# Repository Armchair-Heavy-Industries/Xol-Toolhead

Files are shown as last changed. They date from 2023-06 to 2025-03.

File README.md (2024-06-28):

[][cc-by-nc-sa]

# Xol Toolhead
Xol Toolhead is the evolution of 'Mantis Xol 2' (<https://github.com/Armchair-Engineering/Mantis-Xol>).<br/>
Aimed at modularity and quality of life improvements for installation and serviceability.<br/>
We have left the mantis carriage behind, and thus are now just Xol sans Mantis. Don't worry, it's still a bit ugly. We wouldn't fix that.

Project lead: ko-fi (https://ko-fi.com/O5O5OCC0K) [DW-Tas](https://github.com/DW-Tas)

Join me on Discord (https://discord.gg/armchairengineeringsux)

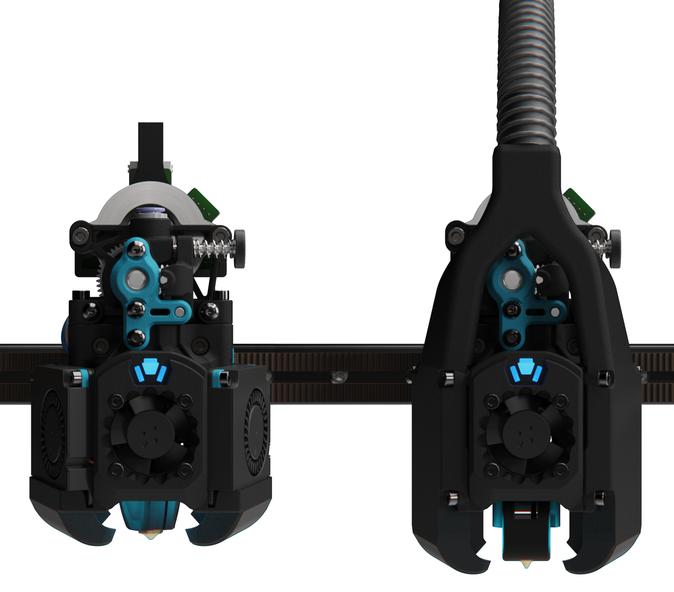
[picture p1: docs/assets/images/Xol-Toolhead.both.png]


## Go to the /docs
All of the documentation has been moved to /docs to help keep the repo organised (crazy I know) and enable future things.
* [Full README](docs/README.md)
  * [Bill of Materials (BOM)](docs/BOM.md)
  * [Printing parts](docs/printing.md)
  * [Carriage assembly](docs/xol_carriage_assembly.md)
  * [Toolhead assembly](docs/toolhead_assembly.md)

<br/><br/>
You can help support the development of Armchair projects.<br/>
Donate at https://ko-fi.com/armchair<br/>
ko-fi (https://ko-fi.com/armchair)
<br/> <br/>

This work is licensed under a
[Creative Commons Attribution-NonCommercial-ShareAlike 4.0 International License][cc-by-nc-sa].

[][cc-by-nc-sa]

[cc-by-nc-sa]: http://creativecommons.org/licenses/by-nc-sa/4.0/
[cc-by-nc-sa-image]: https://licensebuttons.net/l/by-nc-sa/4.0/88x31.png
[cc-by-nc-sa-shield]: https://img.shields.io/badge/License-CC%20BY--NC--SA%204.0-lightgrey.svg

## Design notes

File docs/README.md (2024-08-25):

[][cc-by-nc-sa]

# Xol Toolhead
Xol Toolhead is the evolution of 'Mantis Xol 2' (<https://github.com/Armchair-Engineering/Mantis-Xol>).<br/>
Aimed at modularity and quality of life improvements for installation and serviceability.<br/>
We have left the mantis carriage behind, and thus are now just Xol sans Mantis. Don't worry, it's still a bit ugly. We wouldn't fix that.

Project lead: ko-fi (https://ko-fi.com/O5O5OCC0K) [DW-Tas](https://github.com/DW-Tas)

Join me on Discord (https://discord.gg/armchairengineeringsux)



## What's new
`Xol-Toolhead Release [2024-06-19]`
### Major update
* Quality of life improvements
  * Toolhead
    * Combined multiple printed parts to simplify assembly
    * No more M2 or M2.5 heatset inserts
    * Part cooling fans slide into the top of the ducts are are secured with 2x M2.5x8 SHCS per fan
      * Hardware reduced from 8x M2 heatsets + 8 M2 screws to just 4 M2.5 screws
    * HE Fan now uses 4x M2.5x16 SHCS (previous M2.5x20 should still work)
    * All four hotend mounting screws can now be used with Rapido and Dragon UHF when using Sherpa-Mini Extruder
  * Carriage
    * Xol Carriage is now a single piece print
    * Belt clips are now the Archetype belt clip system
    * Internal path added for probe wires
* BOM changes
  * Toolhead
    * Removed:
      * M2 and M2.5 heatsets (except for X endstop)
      * M2 Screws (except for X endstop)
    * Extruder mount front 2 SHCS now 16mm (previously 20mm)
  * Carriage
    * All versions now attach to MGN rail with M3x8 SHCS (MGN12 previously required M3x6 BHCS)
    * Archetype belt clips require 4mm OD, 0.45mm wall width tube
      * 2x 22.5mm lengths
      * 'Has been tested with 4/3mm PTFE tube and seems OK but harder to install'
    * Belt pins are now all M3x30 for all carriage/belt combinations
      * Cut down screws now OK due to the metal tube protecting the belts
    * Added:
      * Large M3 washers and 2x M3x8 SHCS for MGN Carriage clamps (not optional, required for carriage strength)
* Tool Requirement
  * Tightening the M3 SHCS of the toolhead "feet" to the carriage requires a M2.5 ball head hex driver. `This is due to the requirement to tighten these screws from a slight angle.`
<details>
<summary><strong>Previous updates</strong> [click to expand]</summary>
<br/>

`Xol-Toolhead Release 2023-12-21`
[Historic Repo Link](https://github.com/Armchair-Heavy-Industries/Xol-Toolhead/tree/b5e52d79f11106338cad1ea619fc55be004061d5)
* Quality of life improvements
  * Cable routing holes are now on both sides of the toolhead
  * Cable routing holes can now fit MF3.0 commonly used on hotends
  * Awkward M3 Heatset insert replaced with easier to install M3 hex nut for front extruder mount connection
  * Rapido hotend mounting points rotated to improve wire routing
* Minimal BOM change
  * 1x M3 Hex Nut replaces 1x M3 Heatset Insert
  * 1x M3x6 BHCS replaces 1x M3x8 BHCS
* Reworked Extruder mount to Hotend mount interface
  * Old Hotend mounts will not work with new Extruder mounts and vice-versa

`Xol-Toolhead Release 2023-09-15`
[Historic Repo Link](https://github.com/Armchair-Heavy-Industries/Xol-Toolhead/tree/18acdc784e08c6703e5be316338cb8c8f26e0477)
* Modular approach to hotend mounts and extruders
  * Hotend mounts and extruder mounts are now separate parts
  * Extruder mounts incorporate the old Xol-Carriage or TAP adapter plates (same number of printed parts overall)
  * "Xol with bones" option: Add some screws for extra rigidity in the hotend mount
* Minimal BOM change
  * 1x M3x8 BHCS
  * 1x M3 Heatset
  * Optional "bones"
    * 2x M2x30 SHCS
    * 2x M2 Heatset
* Xol-Carriage update
  * Stronger belt clips
  * bigger probe cable channel with cable tie slot

`Xol-Toolhead Release 2023-07-14`
[Historic Repo Link](https://github.com/Armchair-Heavy-Industries/Xol-Toolhead/tree/bd63772155dfab692449fd498208c855561d44cf)
* Standardised hotend mounts around the Voron Design CW2/TAP carriage bolt hole pattern.
  * This approach reduces the number of hotend mounts and ducts by half - You don't have to search for TAP or non-TAP and we don't have to maintain twice as many parts
* Xol-Carriage
  * A new carriage built for Xol-Toolhead
  * Uses metal pins and a belt clip to secure the belts instead of having them squashed between mgn9/12 carriage and toolhead carriage
  * Improved serviceability - remove the toolhead from the carriage without disassembly in the printer. Unless you use Voron TAP or refuse to buy M2.5 hardware for Xol Carriage. Buy the m2.5 hardware, it's worth it trust us.
  * Modular probe mounting system - change probes without changing the whole carriage _`*Except for KlickyNG`_
* These carriage changes mean you can use any carriage that a Stealthburner bolts onto. (Our Xol-Carriage, or the stock voron carriage even.)
</details>

## Supported hardware
### Hotends
* Rapido HF
* Rapido UHF
* DropEffect XG
* DropEffect NeXtG
* Red Lizard K1-UHF
* Dragon UHF / UHF-Mini
* Dragon Standard / High Flow
* Dragon Ace
* Revo Voron
* NF-Crazy Volcano (or standard with v6 melt zone extender) `NF-Crazy with standard wide block no longer supported without extender`
* Others via User mods including [Bambulab](https://github.com/Armchair-Heavy-Industries/Armchair-Usermods/tree/main/files/Xol-Toolhead/BambuLab_Xol_HE_Mount)

### Extruders
* Sherpa-Mini
* Annex Double Folded Ascender
* Galileo G2SA *
* WristWatch G2 *
* WristWatch BMG
* Escapement (experimental)
* Vz-Hextrudort-Low
* LGX-Lite
* Orbiter v2.0

`⚠️ * G2SA and WWG2 not compatible with XolPAP `

### Probes
* PCB Klicky
* Klicky
* Beacon (Normal)
* Euclid
* Voron Design TAP `For RC8+ we suggest to use m3x50 BHCS instead of SHCS`<br/>
* BTT Eddy
* ⚠️ _KlickyNG support has been removed in this release_

### X-Rail/Belts
* MGN12H - 6mm Belts
* MGN12H - 9mm Belts
* MGN9H - 6mm Belts
* MGN9H - 9mm Belts

> [!WARNING]
> ## Front Idlers  
> Xol-Toolhead can collide with the stock voron front idlers for Trident and 2.4 when the toolhead is in the front corners of the build area. This can cause also issues with the homing sequence when homing X if the toolhead is at the front of the gantry on Y. <br/><br/>
> Fully compatible idlers:<br/>
> * clee's [BFI (Beefy Front Idlers)](https://github.com/clee/VoronBFI)  <br/>
> * Ramalama2's [Front Idlers](https://github.com/Ramalama2/Voron-2-Mods/tree/main/Front_Idlers)  

<br/>

> [!IMPORTANT]
> We've made some instructions for printing and assembly.  
> They took ages to make, please read them.  
> * [Bill of Materials (BOM)](BOM.md)  
> * [Printing parts](printing.md)  
> * [Carriage assembly](xol_carriage_assembly.md)  
> * [Toolhead assembly](toolhead_assembly.md)  
> * [LED Harness](led_harness.md)

## Acknowledgements
* [DW-Tas](https://github.com/DW-Tas) for giving Xol the giant refresh it needed.
* [CorvidBuilds](https://github.com/CorvidBuilds) for Xol1 and Xol2, the predecessors to this project.
* [Long/Mandryd](https://github.com/mandryd/VoronUsers/tree/master/printer_mods/Long/Mantis_Dual_5015) for the Mantis toolhead.
* [Derpimus](https://github.com/lraithel15133) for the exegesis, some CAD work, feedback, and just being a rad dude.
* [KayosMaker](https://github.com/KayosMaker) for the CAN board mounts and spacers.
* [JosAr](https://github.com/jlas1/Klicky-Probe) for Klicky.
* [WhoppingPochard](https://github.com/tanaes) and [VinnyCordeiro](https://github.com/VinnyCordeiro/) for PCB Klicky.
* [Nionio6915](https://github.com/nionio6915/Euclid_Probe) for Euclid.
* [VoronDesign](https://github.com/VoronDesign) for this particular CoreXY flavor.
* [AnnexEngineering](https://github.com/Annex-Engineering) for the Sherpa Mini and Double Folded Ascender extruders, and the K3 that influenced the air management of the ducts. And also for giving access to an early revision of the DFA so it could be adapted for this toolhead.
* [clee](https://github.com/clee), you know what you did.

<br/><br/>
You can help support the development of Armchair projects.<br/>
Donate at https://ko-fi.com/armchair<br/>
ko-fi (https://ko-fi.com/armchair)
<br/> <br/>

This work is licensed under a
[Creative Commons Attribution-NonCommercial-ShareAlike 4.0 International License][cc-by-nc-sa].

[][cc-by-nc-sa]

[cc-by-nc-sa]: http://creativecommons.org/licenses/by-nc-sa/4.0/
[cc-by-nc-sa-image]: https://licensebuttons.net/l/by-nc-sa/4.0/88x31.png
[cc-by-nc-sa-shield]: https://img.shields.io/badge/License-CC%20BY--NC--SA%204.0-lightgrey.svg

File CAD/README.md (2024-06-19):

The custom STLs that enable support for the Annex Double Folded Ascender are derived from an Annex Engineering design, they are bound by their license.
<br/><br/>
Additionally, the "assembly guide" CAD contains a mod of the Anex Sherpa-Mini which is also bound by their license.
<br/><br/>
The License Agreement for these "products" can be found here: https://github.com/Annex-Engineering/ANNEX-Engineering-License-Agreement
<br/><br/>
Product pages for these products can be found at:
* https://github.com/Annex-Engineering/Folded_Ascender-Extruder
* https://github.com/Annex-Engineering/Sherpa_Mini-Extruder

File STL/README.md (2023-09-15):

# Need help deciding what to print?
[Read the printing page](../docs/printing.md)

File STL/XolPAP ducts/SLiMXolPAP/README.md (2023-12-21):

# Completely experimental CPAP drop-in for Xol-Toolhead

* Fits over existing toolhead and screws into same heatsets as the 4010 fans would
* 15mm ID CPAP hose (same as Mellow CPAP for VZ-Bot)
* Changed to a single piece that needs to be printed inverted with supports and support blockers (see images below)
* Standard shaped Xol ducts just powered by a CPAP instead of 4010

If you use this please report your findings to the Xol-Toolhead discord channel.

> [!WARNING]  
> Does not fit with Galileo 2 extruder

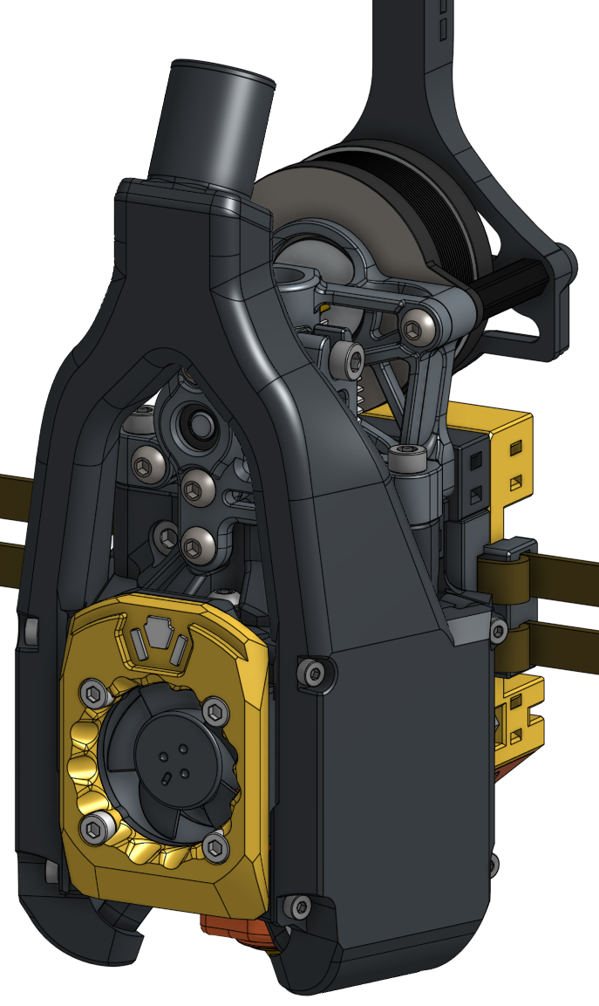
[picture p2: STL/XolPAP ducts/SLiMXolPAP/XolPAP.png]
XolPAP


### Use support blockers like this
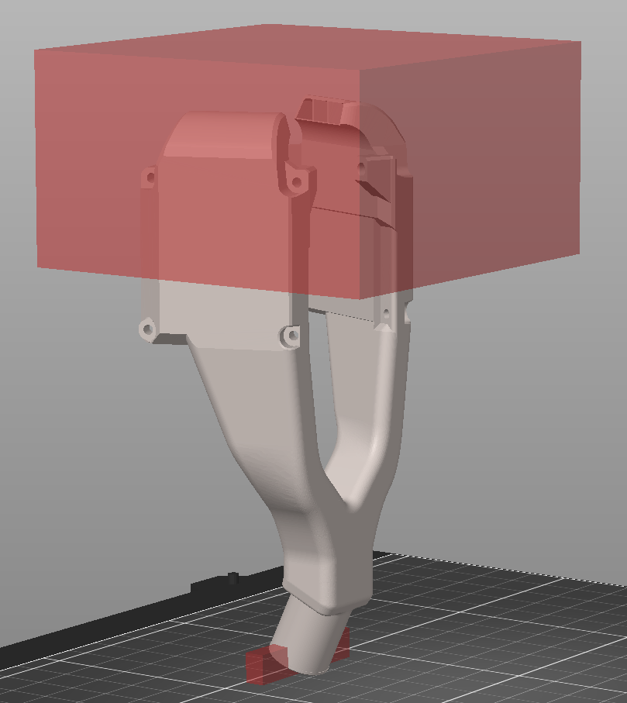
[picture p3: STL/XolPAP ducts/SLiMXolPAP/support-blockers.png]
Support blockers


### Sliced preview
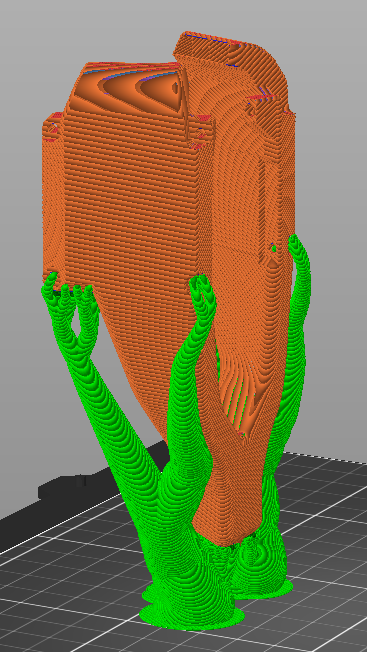
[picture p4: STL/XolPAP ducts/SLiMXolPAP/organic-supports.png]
Organic supports


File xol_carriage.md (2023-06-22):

### Xol Carriage
A new carriage built to allow Xol to standardise around the Voron CW2 (TAP) mounting pattern.
This is in very early stages of development. Parts are subject to change at any time.
Testing and feedback are welcome at the Xol-Toolhead channel on the Armchair Engineering discord. <https://discord.com/channels/1029426383614648421/1046422202460930129>

#### Carriage Design Goals
* Uses same mounting pattern as TAP (reduce Xol permutations)
* Easily remove toolhead from carriage without toolhead disassembly
* Modular approach to probes

#### Additional Hardware
To accommodate design requirements, some additional hardware will be required when using this mount.
Specifically:
* M2.5 heatsets are used in the feet of the Xol hotend mount
* M3 x 25mm pins (30mm for 9mm belt version) are used in the belt attachment system

The dimensions of the M2.5 heatsets are
* thread: M2.5
* Length: 4mm
* Outer Diameter: 3.5mm
(M2.5x4x3.5)

### Acknowledgements
Thanks to the Armchair Engineering team and Voron Design. This carriage is built for Xol but is based heavily on the Voron Design CW2 mounting system.

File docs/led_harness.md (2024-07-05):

# Build instructions for Xol Toolhead LED harness
> [!WARNING]
> ## Sequin PCB thickness   
> The hotend mounts are only compatible with thin PCB board sequins.  
> Known compatible sources:<br/>
> RGBW: [LAB4450 (EU)](https://lab4450.com/product/rgbw-sequins/)<br/>
> RGBW: [Replimat[labs] (EU)](https://www.replimat.eu/4x-rgbw-sequins-for-xol-minisb/rt10179)<br/>
> RGBW: [JB3D.uk (UK)](https://jb3d.uk/product/rgbw-sequin-led-sk6812/)<br/>
> RGB:  [FYSETC (Ali Express)](https://www.aliexpress.com/item/1005006023213341.html)

> [!IMPORTANT]
> ## LED Order
> Wiring as shown will result in the LED order being the same as for the popular StealthBurner LED harness.<br/>
> This should enable the use of popular LED control macros without complex modifications.

| Notes | Image |
|--- | --- |
| Required Tools  | Wire cutters<br/>Wire strippers<br/>Soldering equipment<br/>Helping hands<br/>Crimping tools to suit your connection type |
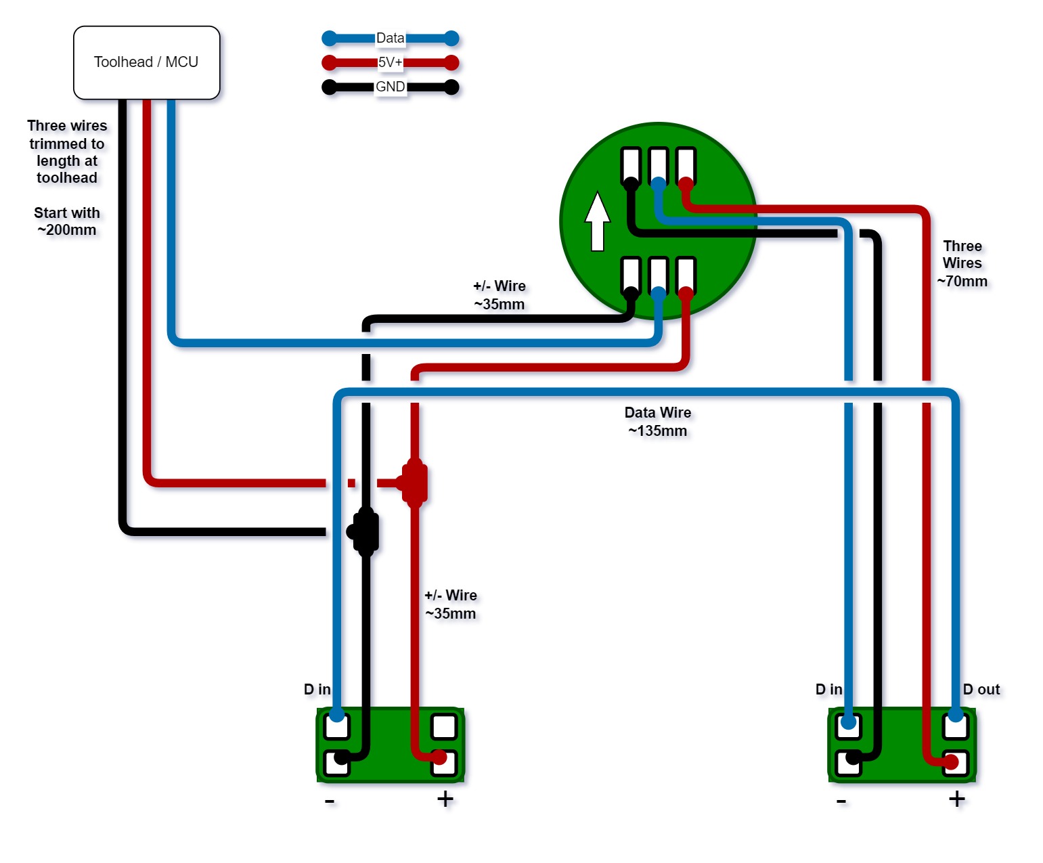
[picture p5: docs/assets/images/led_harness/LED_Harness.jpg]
| Get all the bits together (BoM) <br/><br/>(11x) Lengths of 26 or 28AWG electrical wire:<br/>- (3x) ~200mm `+/-/D` with one end stripped and tinned <br/>- (4x) ~35mm `+/-`with one end stripped and tinned (+/-)<br/>- (3x) 70mm `+/-/D` stripped and tinned at both ends<br/>- (1x) ~135mm `D` stripped and tinned at both ends<br/>(1x) Neopixel LED PCB<br/>(2x) Sequin LED PCB (0.8mm thick PCB board)<br/>JST XH (or similar) connector and pins to suit your printer<br/><br/>`+` = 5V+ wire <br/>`-` = Ground wire<br/>`D` = Data/Signal wire <br/><br/>Lengths given are for a harness that works with either UHF or standard length toolheads |  |
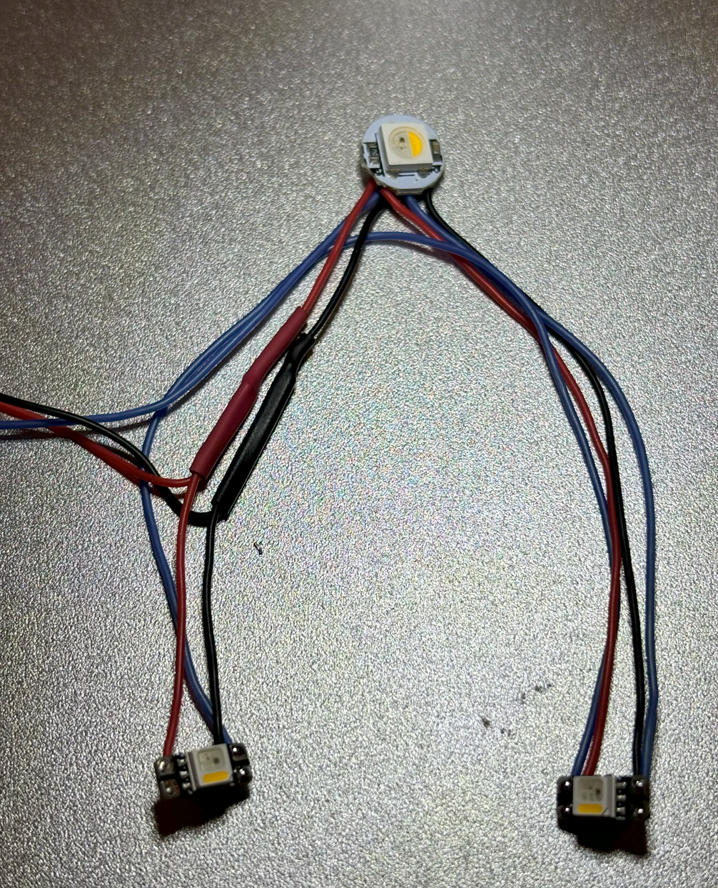
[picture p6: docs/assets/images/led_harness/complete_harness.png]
| Follow the wiring diagram above. <br/> The completed harness should look similar to the photos shown.  <br/><br/> Completed Harness  |  |
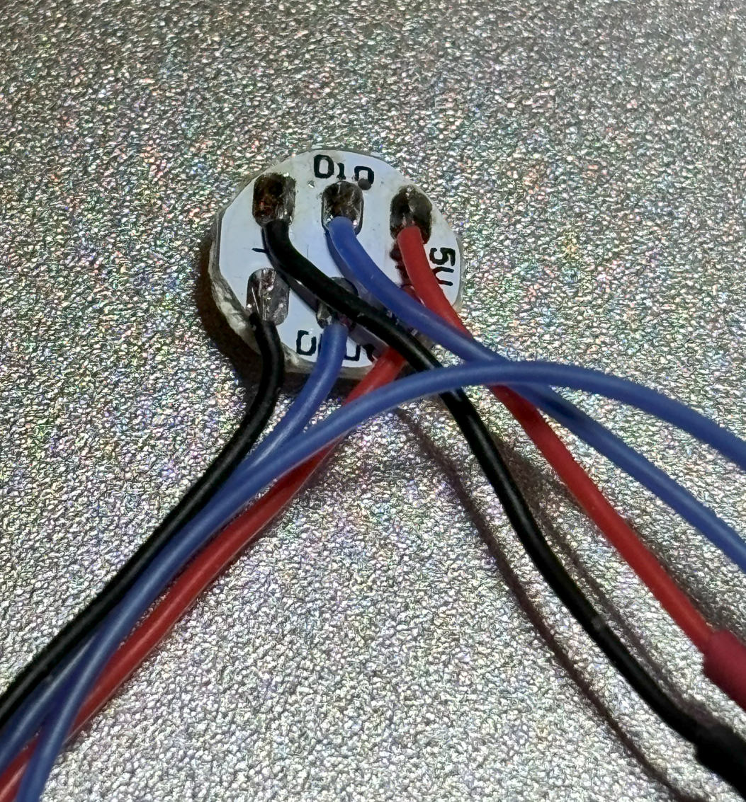
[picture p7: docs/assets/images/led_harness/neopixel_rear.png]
| Neopixel `Status LED` |  |
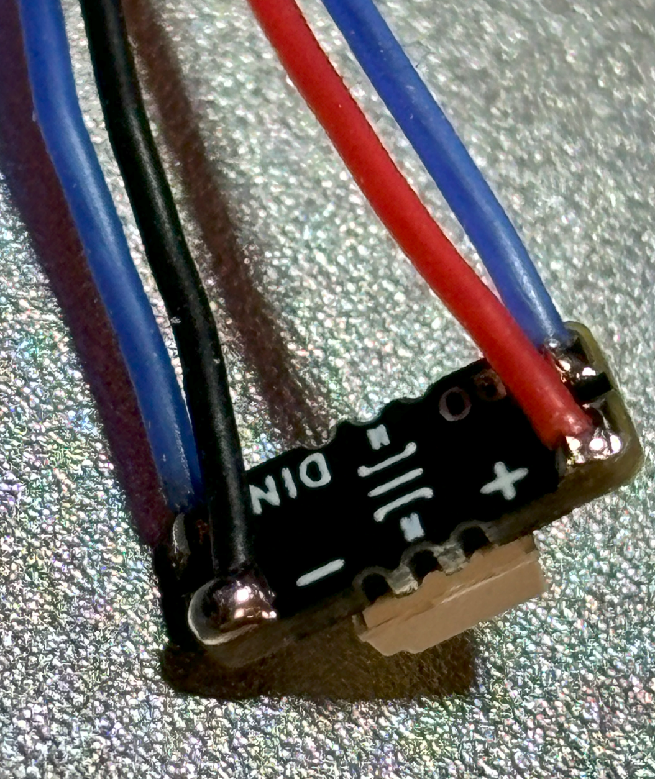
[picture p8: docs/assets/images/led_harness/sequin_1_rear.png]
| Sequin #1 `Part Lighting` |  |
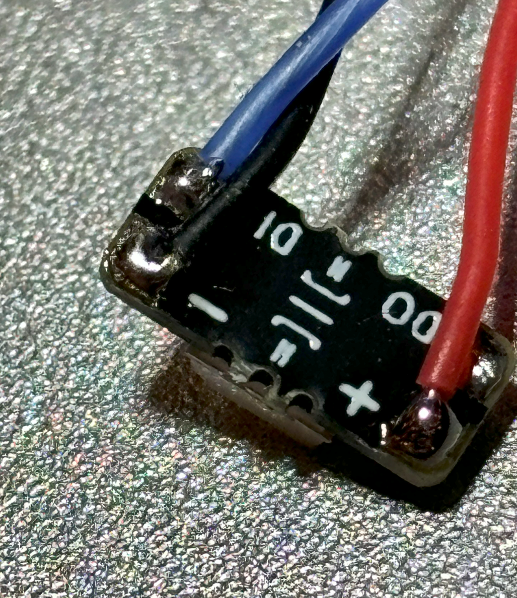
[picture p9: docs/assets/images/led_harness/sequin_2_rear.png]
| Sequin #2 `Part Ligting`  |  |
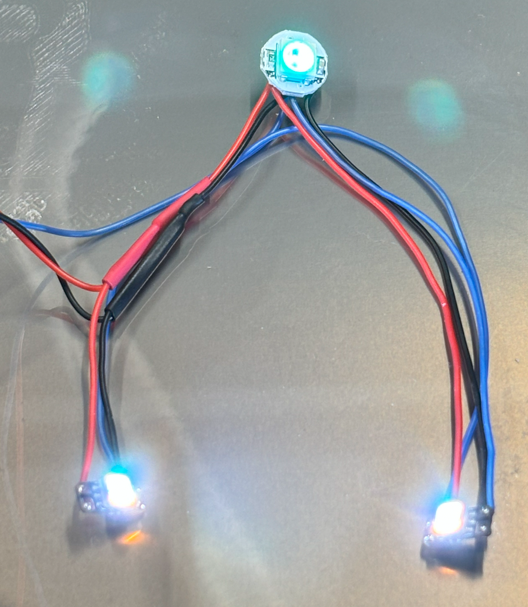
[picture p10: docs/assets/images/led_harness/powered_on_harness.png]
| Powered up! |   |

⬅  [Toolhead assembly](toolhead_assembly.md)

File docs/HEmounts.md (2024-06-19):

[Xol_HE_Mount-Dragon-Ace_Extender_Fan.stl](<../STL/HE Mounts/Xol_HE_Mount-Dragon-Ace_Extender_Fan.stl>)
[Xol_HE_Mount-Dragon-Ace_Extender_XolPAP.stl](<../STL/HE Mounts/Xol_HE_Mount-Dragon-Ace_Extender_XolPAP.stl>)
[Xol_HE_Mount-Dragon-Ace_Fan.stl](<../STL/HE Mounts/Xol_HE_Mount-Dragon-Ace_Fan.stl>)
[Xol_HE_Mount-Dragon-Ace_XolPAP.stl](<../STL/HE Mounts/Xol_HE_Mount-Dragon-Ace_XolPAP.stl>)
[Xol_HE_Mount-DragonSF-HF_Fan.stl](<../STL/HE Mounts/Xol_HE_Mount-DragonSF-HF_Fan.stl>)
[Xol_HE_Mount-DragonSF-HF_XolPAP.stl](<../STL/HE Mounts/Xol_HE_Mount-DragonSF-HF_XolPAP.stl>)
[Xol_HE_Mount-DragonUHF_Fan.stl](<../STL/HE Mounts/Xol_HE_Mount-DragonUHF_Fan.stl>)
[Xol_HE_Mount-DragonUHF_Mini_Fan.stl](<../STL/HE Mounts/Xol_HE_Mount-DragonUHF_Mini_Fan.stl>)
[Xol_HE_Mount-DragonUHF_Mini_XolPAP.stl](<../STL/HE Mounts/Xol_HE_Mount-DragonUHF_Mini_XolPAP.stl>)
[Xol_HE_Mount-DragonUHF_XolPAP.stl](<../STL/HE Mounts/Xol_HE_Mount-DragonUHF_XolPAP.stl>)
[Xol_HE_Mount-NF-Crazy_Volcano_Fan.stl](<../STL/HE Mounts/Xol_HE_Mount-NF-Crazy_Volcano_Fan.stl>)
[Xol_HE_Mount-NF-Crazy_Volcano_XolPAP.stl](<../STL/HE Mounts/Xol_HE_Mount-NF-Crazy_Volcano_XolPAP.stl>)
[Xol_HE_Mount-Rapido_HF_Fan.stl](<../STL/HE Mounts/Xol_HE_Mount-Rapido_HF_Fan.stl>)
[Xol_HE_Mount-Rapido_HF_XolPAP.stl](<../STL/HE Mounts/Xol_HE_Mount-Rapido_HF_XolPAP.stl>)
[Xol_HE_Mount-Rapido_UHF_Fan.stl](<../STL/HE Mounts/Xol_HE_Mount-Rapido_UHF_Fan.stl>)
[Xol_HE_Mount-Rapido_UHF_XolPAP.stl](<../STL/HE Mounts/Xol_HE_Mount-Rapido_UHF_XolPAP.stl>)
[Xol_HE_Mount-Revo-Voron_Fan.stl](<../STL/HE Mounts/Xol_HE_Mount-Revo-Voron_Fan.stl>)
[Xol_HE_Mount-Revo-Voron_XolPAP.stl](<../STL/HE Mounts/Xol_HE_Mount-Revo-Voron_XolPAP.stl>)
[Xol_HE_Mount-XG_Fan.stl](<../STL/HE Mounts/Xol_HE_Mount-XG_Fan.stl>)
[Xol_HE_Mount-XG_XolPAP.stl](<../STL/HE Mounts/Xol_HE_Mount-XG_XolPAP.stl>)

[Xol_HE_Mount-Dragon-Ace_Extender_Fan.stl](<../STL/HE Mounts/Xol_HE_Mount-Dragon-Ace_Extender_Fan.stl>)
[Xol_HE_Mount-Dragon-Ace_Extender_XolPAP.stl](<../STL/HE Mounts/Xol_HE_Mount-Dragon-Ace_Extender_XolPAP.stl>)
[Xol_HE_Mount-Dragon-Ace_Fan.stl](<../STL/HE Mounts/Xol_HE_Mount-Dragon-Ace_Fan.stl>)
[Xol_HE_Mount-Dragon-Ace_XolPAP.stl](<../STL/HE Mounts/Xol_HE_Mount-Dragon-Ace_XolPAP.stl>)
[Xol_HE_Mount-DragonSF-HF_Fan.stl](<../STL/HE Mounts/Xol_HE_Mount-DragonSF-HF_Fan.stl>)
[Xol_HE_Mount-DragonSF-HF_XolPAP.stl](<../STL/HE Mounts/Xol_HE_Mount-DragonSF-HF_XolPAP.stl>)
[Xol_HE_Mount-DragonUHF_Fan.stl](<../STL/HE Mounts/Xol_HE_Mount-DragonUHF_Fan.stl>)
[Xol_HE_Mount-DragonUHF_Mini_Fan.stl](<../STL/HE Mounts/Xol_HE_Mount-DragonUHF_Mini_Fan.stl>)
[Xol_HE_Mount-DragonUHF_Mini_XolPAP.stl](<../STL/HE Mounts/Xol_HE_Mount-DragonUHF_Mini_XolPAP.stl>)
[Xol_HE_Mount-DragonUHF_XolPAP.stl](<../STL/HE Mounts/Xol_HE_Mount-DragonUHF_XolPAP.stl>)
[Xol_HE_Mount-NF-Crazy_Volcano_Fan.stl](<../STL/HE Mounts/Xol_HE_Mount-NF-Crazy_Volcano_Fan.stl>)
[Xol_HE_Mount-NF-Crazy_Volcano_XolPAP.stl](<../STL/HE Mounts/Xol_HE_Mount-NF-Crazy_Volcano_XolPAP.stl>)
[Xol_HE_Mount-Rapido_HF_Fan.stl](<../STL/HE Mounts/Xol_HE_Mount-Rapido_HF_Fan.stl>)
[Xol_HE_Mount-Rapido_HF_XolPAP.stl](<../STL/HE Mounts/Xol_HE_Mount-Rapido_HF_XolPAP.stl>)
[Xol_HE_Mount-Rapido_UHF_Fan.stl](<../STL/HE Mounts/Xol_HE_Mount-Rapido_UHF_Fan.stl>)
[Xol_HE_Mount-Rapido_UHF_XolPAP.stl](<../STL/HE Mounts/Xol_HE_Mount-Rapido_UHF_XolPAP.stl>)
[Xol_HE_Mount-Revo-Voron_Fan.stl](<../STL/HE Mounts/Xol_HE_Mount-Revo-Voron_Fan.stl>)
[Xol_HE_Mount-Revo-Voron_XolPAP.stl](<../STL/HE Mounts/Xol_HE_Mount-Revo-Voron_XolPAP.stl>)
[Xol_HE_Mount-XG_Fan.stl](<../STL/HE Mounts/Xol_HE_Mount-XG_Fan.stl>)
[Xol_HE_Mount-XG_XolPAP.stl](<../STL/HE Mounts/Xol_HE_Mount-XG_XolPAP.stl>)

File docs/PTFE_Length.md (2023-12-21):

# PTFE tube length by Hotend/Extruder
All measurements are in mm

| Hotend | Sherpa-Mini \*printed | DFA\*\* | VZ-Hextrudort-Low | LGX-Lite | Orbiter v2.0 |
| --- | --- | --- | --- | --- | --- |
| Rapido | 36.5 | 33.2 | 43.2 | 39.2 | 43.0 |
| Dragon ST/HF | 31 | 27.7 | 37.7 | 33.7 | 37.5 |
| Dragon UHF/Mini | 21.5 | 18.2 | 28.2 | 24.2 | 28.0 |
| DropEffect XG/NeXt-G | 22.5 | 19.2 | 29.2 | 25.2 | 29.0 |
| Red Lizard K1-UHF | 22.5 | 19.2 | 29.2 | 25.2 | 29.0 |
| NF Craxy | 22.5 | 19.2 | 29.2 | 25.2 | 29.0 |
| Revo Voron | 28.9 | 25.6 | 35.6 | 31.6 | 35.3 |

`*Sherpa-Mini CNC has been measured as 2mm shorter, but there may be variations by manufacturer`<br/>
`**DFA measurements are to the top of the chamfer inside the extruder bottom. You will need to chamfer the top of the PTFE tube or shorten by 1mm`<br/>
`***All of these measurements are based off CAD. It is always best to measure and cut to length based on your own setup`

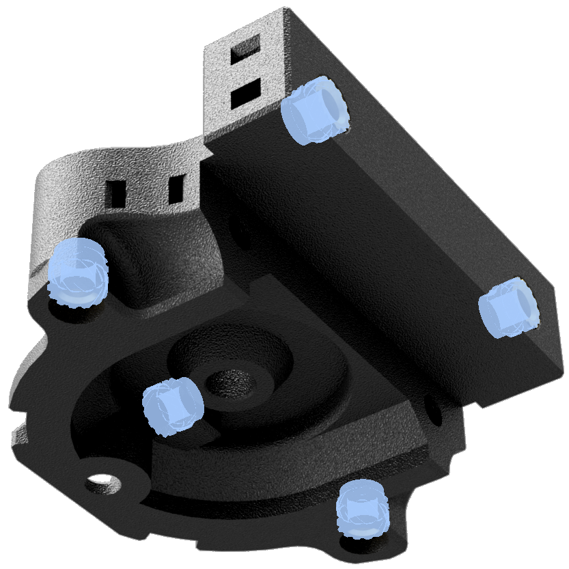
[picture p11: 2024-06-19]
docs/assets/images/xol_toolhead/extruder_mount_heatsets.png

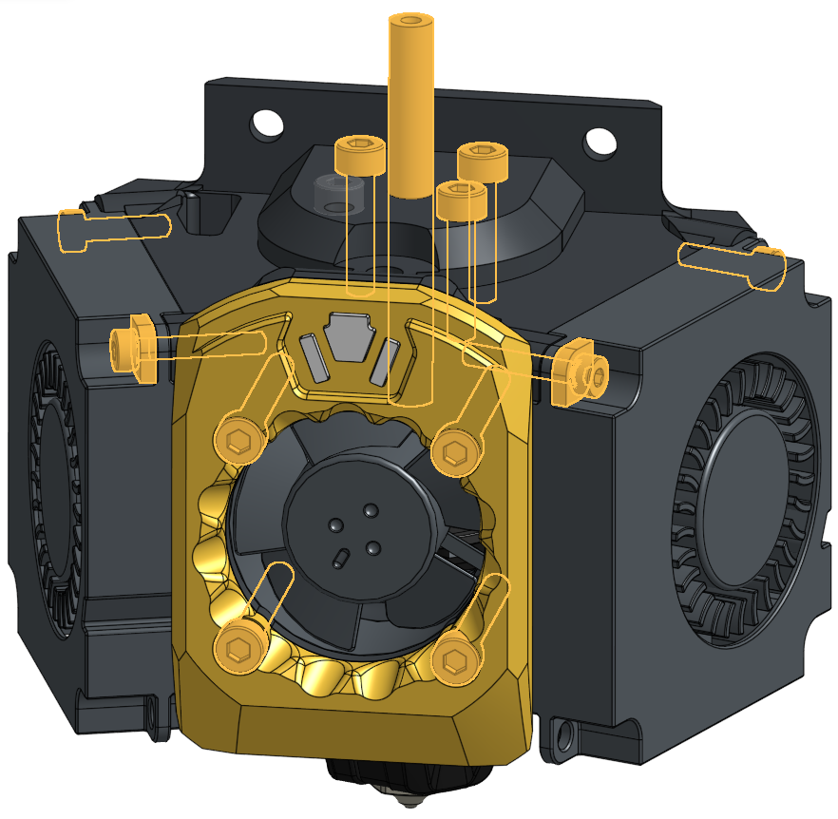
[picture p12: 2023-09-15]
docs/assets/images/tap_toolhead/lower_toolhead_no_ducts.png

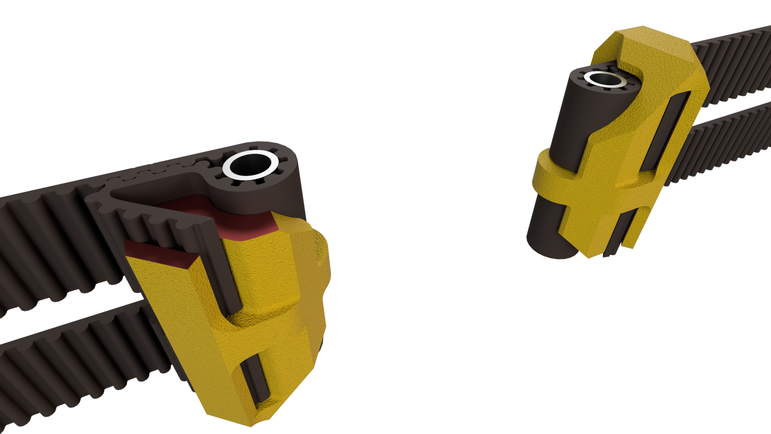
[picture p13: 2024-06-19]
docs/assets/images/xol_carriage/9mm_belts_and_clips.png

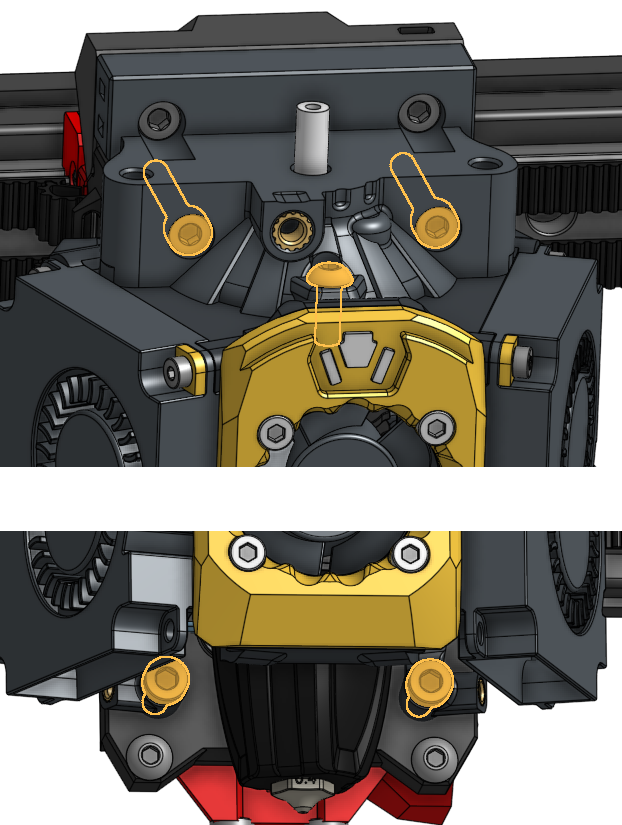
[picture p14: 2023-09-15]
docs/assets/images/tap_toolhead/hotend_mount_to_TAP.png

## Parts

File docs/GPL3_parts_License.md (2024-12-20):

The custom STLs that come from GPL3 projects remain under the GPLv3 license.
<br/><br/>
These parts are:
* STL\Extruder Mounts\G2SA front for Xol Extruder Mount.stl (CAD\parts\G2SA front for Xol Extruder Mount.step)
* STL\Extruder Mounts\WWG2 front for Xol Extruder Mount.stl (CAD\parts\WWG2 front for Xol Extruder Mount.step)

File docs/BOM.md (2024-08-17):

# Xol Toolhead Bill of Materials (BOM)
Read **ALL** of the sections below to understand your hardware requirements, there's some bits here that aren't on a standard Voron build BOM.
The chances are that something was missed, but if you have a good mix of M2, M2.5 and M3 hardware you'll probably still end up with a working printer.

## Carriage

#### Required Hardware
| Qty | Item | Notes |
| --- | --- | --- |
| 5 | M3 Heatset Insert | Standard Voron spec: 5mm Outer Diameter x 4mm Length |
| 6 | M3 x 8 SHCS | 4x MGN carriage mounting, 2x MGN carriage clamps |
| 4 | M3 Hex Nut | 2x MGN carriage clamps, 2x toolhead mounting |
| 2 | M3 DIN9021 flat washer  | MGN Carriage clamping. `Alternatively use M3 + M5 stacked washers` |
| 2 | M3 x 30 Pin | Belt mounting system |
| 2 | Hollow metal tube: 4mm OD, 3.1 to 3.2mm ID,  22 to 22.5mm length. | 4mm OD, 0.45mm wall width (0.4mm wall width is OK). Stainless steel, brass, aluminium all tested OK. Used for belt mounting system.`4mm OD/3mm ID PTFE tube can be used temporarily` |
| 2 | 1.8mm wide cable tie or 0.5mm solid core wire | To attach M4 tube to belt clips as per Archetype clips |

#### Probe/Extruder Hardware
Follow probe or extruder instructions for required hardware.

`* If using Voron Design TAP RC8+ it is recommended to replace the two M3 x 50 SHCS with M3 x 50 BHCS to improve build plate clearance.`

## Toolhead

#### Required Hardware
| Qty | Item | Notes |
| --- | --- | --- |
| 3*  | M3 Heatset Insert | Standard Voron spec: 5mm Outer Diameter x 4mm Length <br/> * Extruder Mount `3rd heatset for extruders with additional front screw` |
| 3 | M3 Hex Nut | 2x Extruder Mount <br/>1x Hotend Mount mount below front of Extruder Block |
| 2 | M3 x 20 Metal Stand-off | CAN/EBB Mounting |
| 2 | M3 x [20][8] SHCS | Extruder to HE Mount. Length varies depending on extruder used <br/> `M3x20 used for Sherpa-Mini, M3x8 used for most others` |
| 6 | M3 x 16 SHCS | 2x Through Extruder and hotend mounts to carriage <br />2x Extruder stepper to standoff <br/>2x CAN/EBB36 mount |
| 7 | M3 x 8 SHCS | 2x HE Mount feet, 2x HE Adapter to carriage, 2x MGN carriage clamping, 1x EBB Mount |
| 2*  | M3 x 6 BHCS | Extruder Mount to Hotend Mount at front. `*additional 1 if using extruder with front faceplate that includes extra point.` |
| 4 | M2.5 x 16 SHCS | HE Fan |
| 4 | M2.5 x 8 SHCS | Part cooling fan mounting |
| 4*  | M2.5 x 8 SHCS | *additional to above if using XolPAP ducts |
| 1 | Short PTFE tube | Between extruder and hotend |

#### Fans
> :information_source: **Understand your electronics and voltages** <br/>
> Do you have the correct voltage at your toolhead or will you need a converter?<br/>
> If using the _recommended_ parts you need 5v, 12v and 24v at the toolhead.

| Qty | Fan Type | Recommended Fan | Notes |
| --- | --- | --- | --- |
| 1 | 2510 Axial Fan <br/> Hotend Fan | Delta Electronics 5v <br/> ASB02505SHA-AY6B | <a href="https://www.digikey.com/en/products/detail/delta-electronics/ASB02505SHA-AY6B/7491489">Purchase Link</a> <br/> `This fan is highly recommended in heated chambers`<br/>`No other 2510 fan comes close to the performance`<br/>`of this fan.` |
| 2 | 4010 Blower Fan <br/> Part Cooling Fans | Delta Electronics <br/> BFB0412HHA-A (12V) <a href="https://www.digikey.com/en/products/detail/delta-electronics/BFB0412HHA-A/2560487">Purchase Link</a> <br/> BFB0405HHA-A (5V)  <a href="https://www.digikey.com/en/products/detail/delta-electronics/BFB0405HHA-A/1014444">Purchase Link</a> <br/> | `24v GDStime fans are fine and many have used them successfully.`<br/>`The Deltas, however, have better durability`<br/>`in heated chambers and always hit their performance claims.`<br/>`It's not uncommon for other fan manufacturers`<br/>`to overstate performance, GDStime included.` |
| 1*  | 7040 or other suitable CPAP remote cooling fan | | XolPAP only |
| 1*  | 15mm ID CPAP flexible hose | | XolPAP only |

Additional notes: Delta's 5V and 12V variants provide the same airflow, pick whichever suits your setup better. If you only have 24V available, you can use a 24V-12V buck converter or run an additional wire in your umbilical for 12v+.

#### Optional Hardware
| Qty | Item | Notes |
| --- | --- | --- |
| 1 | M3 Heatset Insert | Sherpa-Mini and G2 / WristWatch front plate attachment |
| 1 | M3 Heatset Insert | DFA Custom bottom |
| 2 | M2 x 10 self tapping screws | X End stop |
| 1 | LED harness | 1x RGB Neopixel LEDs, and <br/> 2x RGB Sequin LEDs (0.8mm board thickness) <br/> 26 or 28 AWG wire. <br/> [Build instructions](led_harness.md)<br/>`Only compatible with the thin PCB board sequins.`<br/>`Known working sources:`<br/>RGBW: [LAB4450 (EU)](https://lab4450.com/product/rgbw-sequins/)<br/>RGBW: [Replimat[labs] (EU)](https://www.replimat.eu/4x-rgbw-sequins-for-xol-minisb/rt10179)<br/>RGBW: [JB3D.uk (UK)](https://jb3d.uk/product/rgbw-sequin-led-sk6812/)<br/>RGB:  [FYSETC (Ali Express)](https://www.aliexpress.com/item/1005006023213341.html) |

<br/><br/><br/><br/>
⬅ [README](README.md) - [Printed Parts](printing.md) ➡

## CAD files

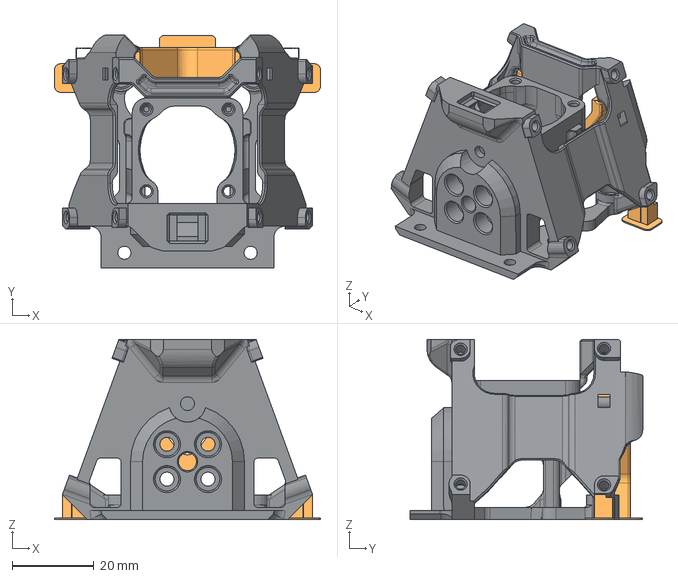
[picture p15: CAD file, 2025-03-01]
CAD/parts/Xol_HE_Mount-Revo-Voron_XolPAP.step
64.9 x 56.8 x 44.0 mm
Support
Xol_HE_Mount-Revo-Voron_XolPAP

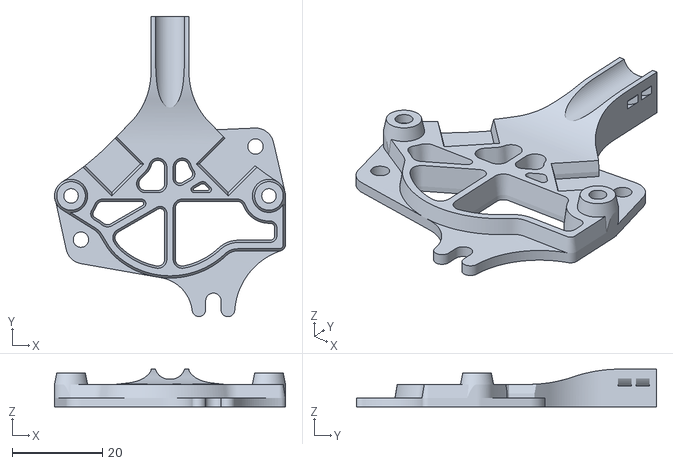
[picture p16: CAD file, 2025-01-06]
STL/EBB Mounts/EBB36 Mount -WWBMG [strain relief].stl
51.2 x 66.5 x 8.36

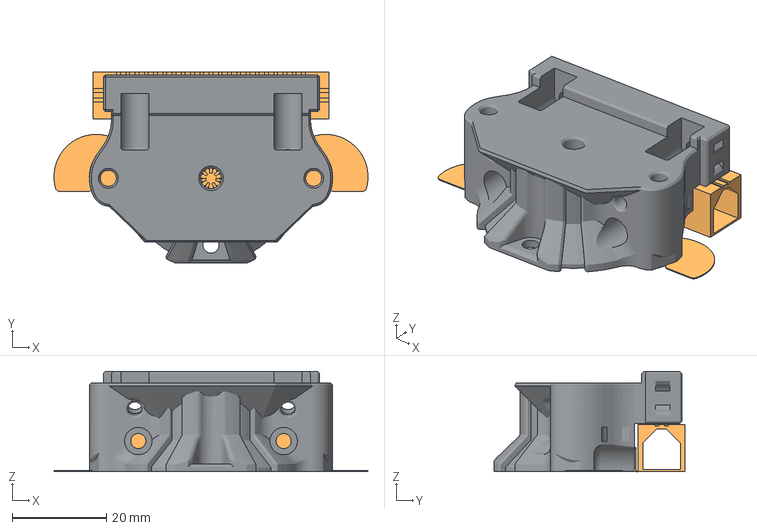
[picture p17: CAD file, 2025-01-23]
STL/Extruder Mounts/Xol Extruder Mount - WW-BMG [Sherpa-Mini Spacing] - TAP.3mf
66.5 x 40.6 x 21.2 mm

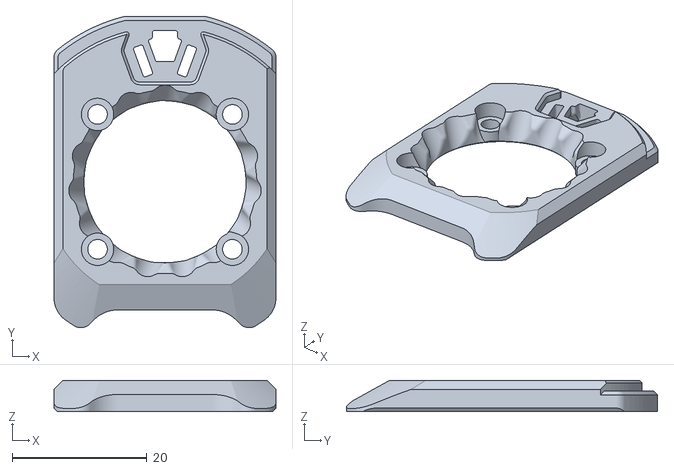
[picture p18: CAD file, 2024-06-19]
STL/Faceplate/Faceplate.stl
32.9 x 46.2 x 4.60

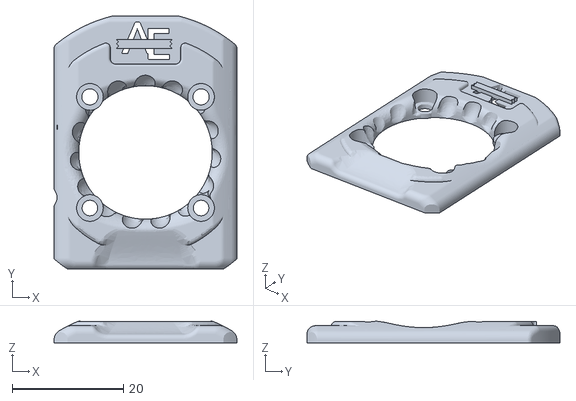
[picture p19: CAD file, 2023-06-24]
STL/Faceplates/Faceplate - LED - Front [southern hemisphere edition].stl
32.9 x 45.5 x 3.89

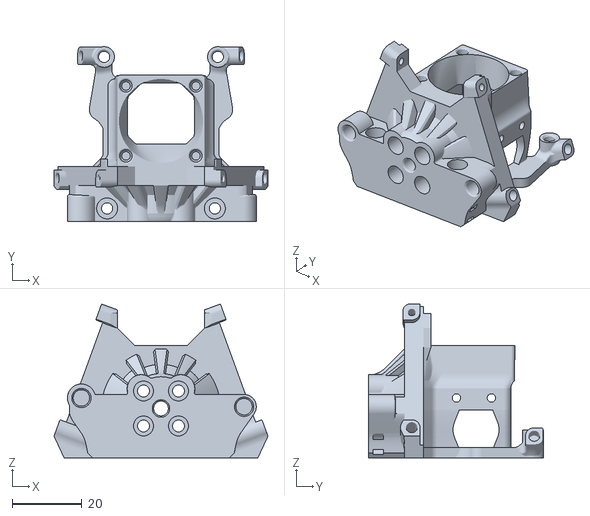
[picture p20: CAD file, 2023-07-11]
STL/HE Mounts/Xol HE Mount - NeXt-G - DFA - fan HS.stl
61.2 x 49.9 x 44.0

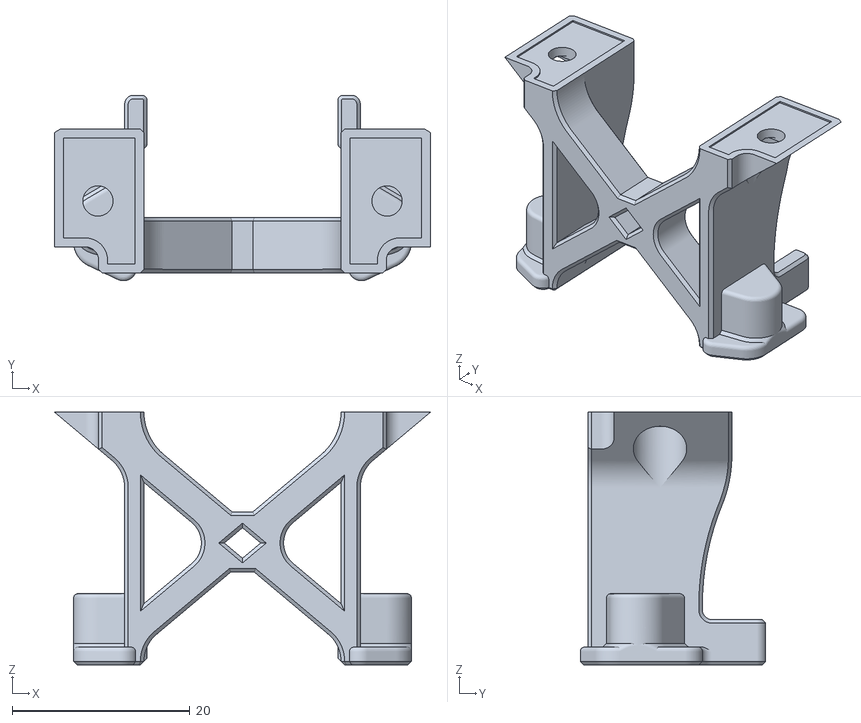
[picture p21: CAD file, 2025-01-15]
STL/Xol-Carriage/Probe Modules/Beacon_RevD+Cartographer_Module_UHF.stl
42.3 x 20.8 x 28.4

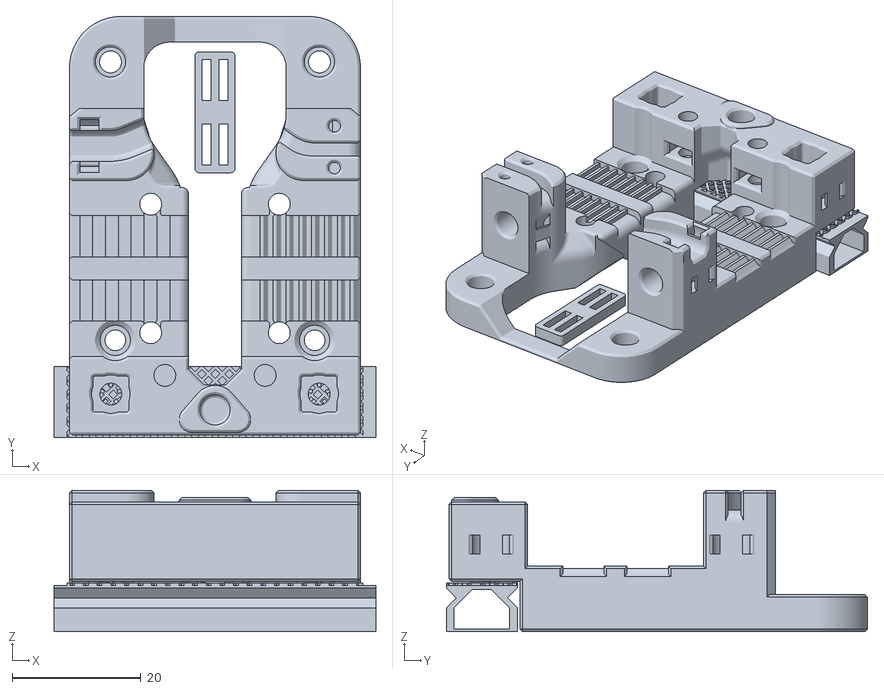
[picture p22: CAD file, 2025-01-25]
STL/Xol-Carriage/Xol-Carriage_MGN12H_6mm_basic_belts.stl
50.1 x 65.5 x 22.0

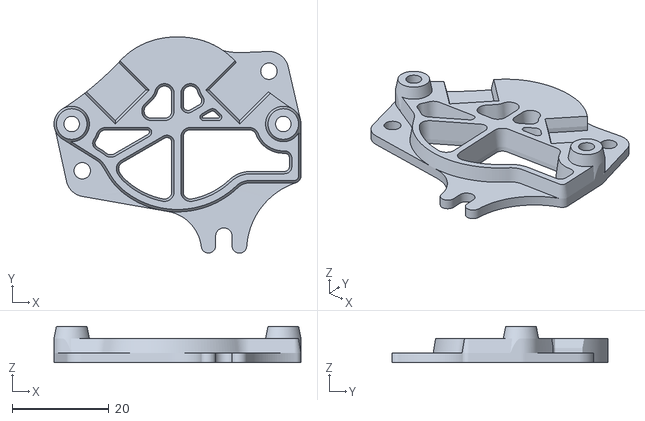
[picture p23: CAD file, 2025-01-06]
STL/EBB Mounts/EBB36 Mount - WWBMG.stl
51.2 x 44.8 x 7.50

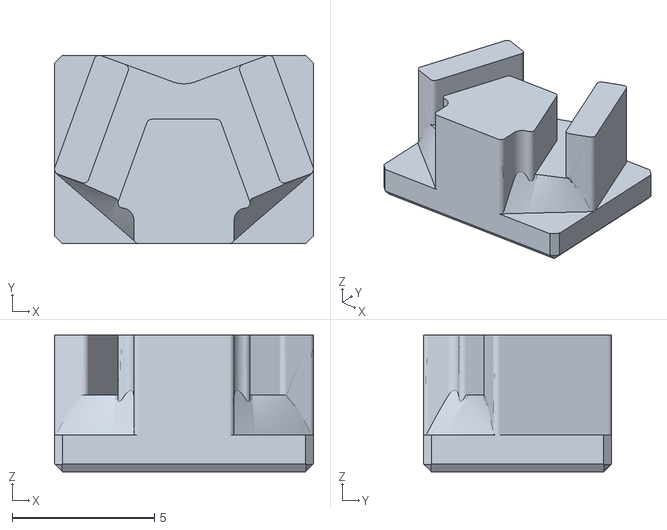
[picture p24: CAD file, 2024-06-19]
STL/Faceplate/[t] Logo LED diffuser.stl
9.09 x 6.61 x 4.80

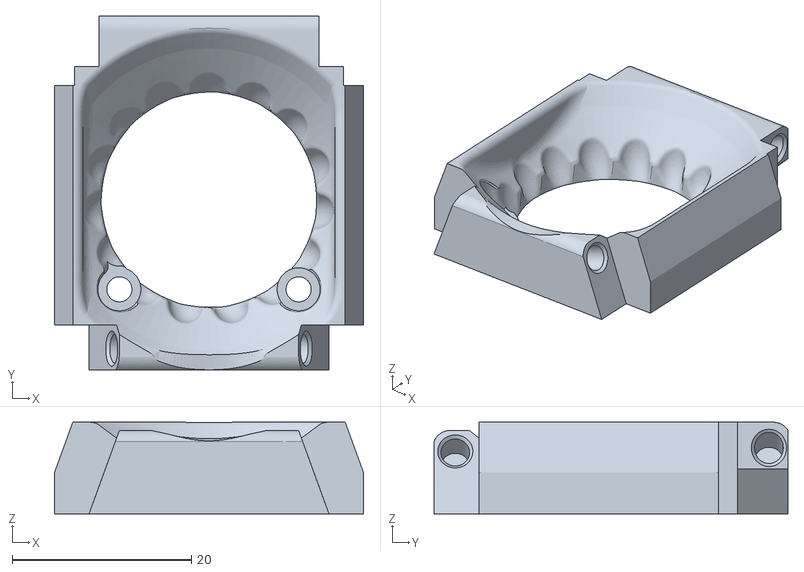
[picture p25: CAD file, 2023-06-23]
STL/Faceplates/Faceplate - standard - XG.stl
34.5 x 39.5 x 10.2

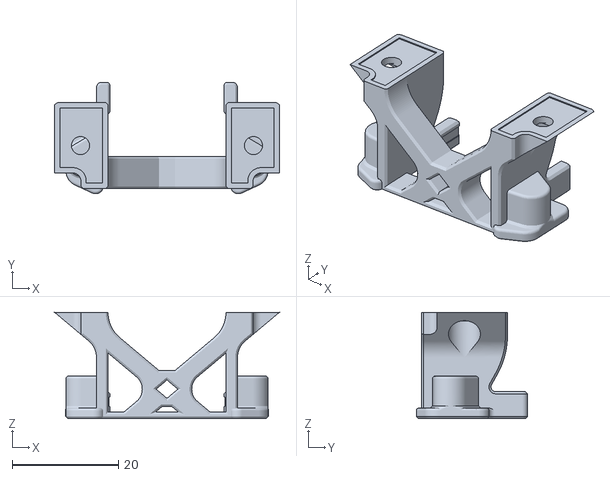
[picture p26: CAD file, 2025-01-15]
STL/Xol-Carriage/Probe Modules/Beacon_RevD+Cartographer_Module.stl
42.3 x 20.9 x 20.0

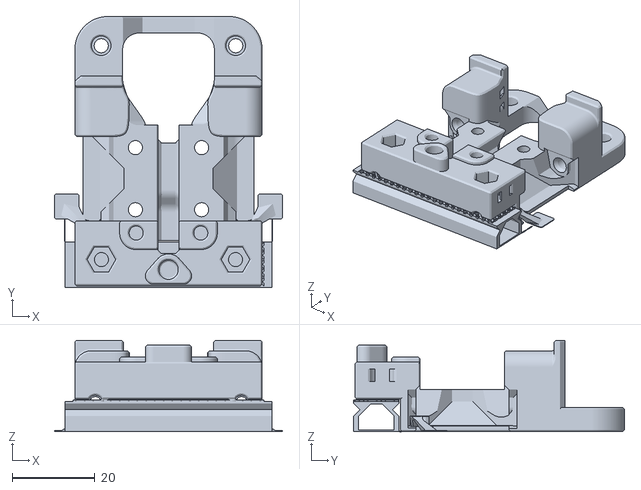
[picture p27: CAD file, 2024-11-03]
STL/Xol-Carriage/Xol-Carriage_MGN9H_PFA-No_X_Endstop.stl
55.2 x 65.5 x 22.0

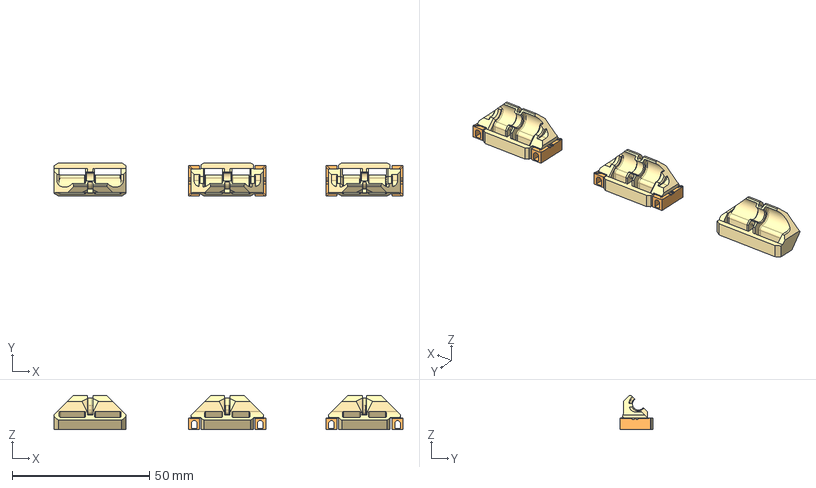
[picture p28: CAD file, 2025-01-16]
CAD/parts/Xol-Carriage Belt Clip Parts.step
127.2 x 12.2 x 12.4 mm

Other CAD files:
CAD/parts/Xol-Carriage_MGN12H_6mm_basic_belts.step
STL/Extruder Mounts/Xol Extruder Mount - WW-BMG [Sherpa-Mini Spacing].3mf
STL/EBB Mounts/EBB36 Mount - VZ-Hextrudort-Low.stl
STL/Extruder Mounts/Xol Extruder Mount - Escapement.stl
CAD/parts/G2SA front for Xol Extruder Mount.step
CAD/parts/WWBMG front for Xol Extruder Mount.step
CAD/parts/WWG2 front for Xol Extruder Mount.step
CAD/parts/Xol Extruder Mount - DFA.step
CAD/parts/Xol Extruder Mount - Escapement - TAP.step
CAD/parts/Xol Extruder Mount - Escapement.step
CAD/parts/Xol Extruder Mount - G2SA - TAP.step
CAD/parts/Xol Extruder Mount - G2SA.step
CAD/parts/Xol Extruder Mount - Orbiter V2 - TAP.step
CAD/parts/Xol Extruder Mount - Orbiter V2.step
CAD/parts/Xol Extruder Mount - Sherpa Mini - TAP.step
CAD/parts/Xol Extruder Mount - Sherpa-Mini.step
CAD/parts/Xol Extruder Mount - VZ-Hex+LGX-L - TAP.step
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

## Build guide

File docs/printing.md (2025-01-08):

# Printing Xol Parts

### Xol parts are not scaled to suit any particular filament. You will need to calibrate your printer/filament appropriately before printing Xol Parts

It is recommended to print a calibration part of a known size and adjust slicer shrinkage compensation.

### Printer tuning
Making Xol easier to assemble also meant making the main hotend mount part a more difficult print. You will need to have a reasonably well callibrated printer (although it was tested on a barely tuned Ender 3). <br/>
Some things in particular to note:
* Support removal `If you're printing too hot or with insufficient cooling the built in supports may be difficult to remove.`
* Overhangs `They're not too steep, but will be a problem if you're not printing your perimeters "inside to outside".`
* Wall widths `Some of the supports have a built in "interface" layers. Make sure your printer profile allows printing of walls down to at least 0.4mm. Check that you can see them in your slicer before you print them. DO NOT use walls wider than 0.55mm`

## What to print
There are many combinations of carriages/hotends/extruders that can be used with Xol. The tables below outline what you should print.

### Carriage
#### Xol Carriage
Pick the parts you need from the lists below and follow the instructions in [xol_carriage_assembly.md](xol_carriage_assembly.md) to build.

Carriage Size
* MGN12H: [Xol-Carriage_MGN12H.stl](../STL/Xol-Carriage/Xol-Carriage_MGN12H.stl)
* MGN9H: [Xol-Carriage_MGN9H.stl](../STL/Xol-Carriage/Xol-Carriage_MGN9H.stl)
* MGN9H (Front rail Printers for Ants [PFA]): [Xol-Carriage_MGN9H_PFA.stl](../STL/Xol-Carriage/Xol-Carriage_MGN9H_PFA.stl)

Belt Width
* 6MM: [[a]_belt_clamp_6mm_x2.stl](../STL/Xol-Carriage/[a]_belt_clamp_6mm_x2.stl)
* 9MM: [[a]_belt_clamp_9mm_x2.stl](../STL/Xol-Carriage/[a]_belt_clamp_9mm_x2.stl)
* 6MM (Front rail Printers for Ants [PFA]): [[a]_belt_clamp_6mm_PFA_x2.stl](../STL/Xol-Carriage/[a]_belt_clamp_6mm_PFA_x2.stl)

Probe Modules
* Pick the module to match your supported probe from the [Probe Modules](<../STL/Xol-Carriage/Probe Modules>) folder. <br/>
`Probe length should match the hotend length (standard or UHF)`

#### Voron Design TAP
Follow instructions from Voron Design <br /> _`For TAP RC8, replace the M3x50 SCHS with M3x50 BHCS to avoid bed clearance issues with regular length Xol Ducts`_

### Hotend Mount
Pick one option from the table below, depending of if you're using 4010 blower fans or remote cooling (XolPAP) for part cooling.

| Hotend | 4010 Blower | XolPAP (Remote Cooling) | Duct Length (for probe module / XolPAP) |
| --- | --- | --- | --- |
| Rapido HF | [Xol_HE_Mount-Rapido_HF_Fan.stl](<../STL/HE Mounts/Xol_HE_Mount-Rapido_HF_Fan.stl>) <br/><br/> [Xol_HE_Mount-Rapido_v2_HF_Fan.stl](<../STL/HE Mounts/Xol_HE_Mount-Rapido_v2_HF_Fan.stl>) | [Xol_HE_Mount-Rapido_HF_XolPAP.stl](<../STL/HE Mounts/Xol_HE_Mount-Rapido_HF_XolPAP.stl>) <br/><br/> [Xol_HE_Mount-Rapido_v2_HF_XolPAP.stl](<../STL/HE Mounts/Xol_HE_Mount-Rapido_v2_HF_XolPAP.stl>) | Standard |
| Rapido UHF | [Xol_HE_Mount-Rapido_UHF_Fan.stl](<../STL/HE Mounts/Xol_HE_Mount-Rapido_UHF_Fan.stl>) <br/><br/> [Xol_HE_Mount-Rapido_v2_UHF_Fan.stl](<../STL/HE Mounts/Xol_HE_Mount-Rapido_v2_UHF_Fan.stl>) | [Xol_HE_Mount-Rapido_UHF_XolPAP.stl](<../STL/HE Mounts/Xol_HE_Mount-Rapido_UHF_XolPAP.stl>) <br/><br/> [Xol_HE_Mount-Rapido_v2_UHF_XolPAP.stl](<../STL/HE Mounts/Xol_HE_Mount-Rapido_v2_UHF_XolPAP.stl>) | UHF |
| DropEffect XG | [Xol_HE_Mount-XG_Fan.stl](<../STL/HE Mounts/Xol_HE_Mount-XG_Fan.stl>) | [Xol_HE_Mount-XG_XolPAP.stl](<../STL/HE Mounts/Xol_HE_Mount-XG_XolPAP.stl>) | Standard |
| DropEffect NeXtG (without extender) | [Xol_HE_Mount-DragonSF-HF_Fan.stl](<../STL/HE Mounts/Xol_HE_Mount-DragonSF-HF_Fan.stl>) | [Xol_HE_Mount-DragonSF-HF_XolPAP.stl](<../STL/HE Mounts/Xol_HE_Mount-DragonSF-HF_XolPAP.stl>) | Standard |
| DropEffect NeXtG (with extender) | [Xol_HE_Mount-DragonUHF_Mini_Fan.stl](<../STL/HE Mounts/Xol_HE_Mount-DragonUHF_Mini_Fan.stl>) | [Xol_HE_Mount-DragonUHF_Mini_XolPAP.stl](<../STL/HE Mounts/Xol_HE_Mount-DragonUHF_Mini_XolPAP.stl>) | Standard |
| Red Lizard K1-UHF | [Xol_HE_Mount-Rapido_UHF_Fan.stl](<../STL/HE Mounts/Xol_HE_Mount-Rapido_UHF_Fan.stl>) | [Xol_HE_Mount-Rapido_UHF_XolPAP.stl](<../STL/HE Mounts/Xol_HE_Mount-Rapido_UHF_XolPAP.stl>) | UHF |
| Dragon UHF | [Xol_HE_Mount-DragonUHF_Fan.stl](<../STL/HE Mounts/Xol_HE_Mount-DragonUHF_Fan.stl>) | [Xol_HE_Mount-DragonUHF_XolPAP.stl](<../STL/HE Mounts/Xol_HE_Mount-DragonUHF_XolPAP.stl>) | UHF |
| Dragon UHF-Mini (extender removed)  | [Xol_HE_Mount-DragonUHF_Mini_Fan.stl](<../STL/HE Mounts/Xol_HE_Mount-DragonUHF_Mini_Fan.stl>) | [Xol_HE_Mount-DragonUHF_Mini_XolPAP.stl](<../STL/HE Mounts/Xol_HE_Mount-DragonUHF_Mini_XolPAP.stl>) | Standard |
| Dragon Standard / High Flow | [Xol_HE_Mount-DragonSF-HF_Fan.stl](<../STL/HE Mounts/Xol_HE_Mount-DragonSF-HF_Fan.stl>) | [Xol_HE_Mount-DragonSF-HF_XolPAP.stl](<../STL/HE Mounts/Xol_HE_Mount-DragonSF-HF_XolPAP.stl>) | Standard |
| Dragon Ace (without extender) | [Xol_HE_Mount-Dragon-Ace_Fan.stl](<../STL/HE Mounts/Xol_HE_Mount-Dragon-Ace_Fan.stl>) | [Xol_HE_Mount-Dragon-Ace_XolPAP.stl](<../STL/HE Mounts/Xol_HE_Mount-Dragon-Ace_XolPAP.stl>) | Standard |
| Dragon Ace (with extender) | [Xol_HE_Mount-Dragon-Ace_Extender_Fan.stl](<../STL/HE Mounts/Xol_HE_Mount-Dragon-Ace_Extender_Fan.stl>) | [Xol_HE_Mount-Dragon-Ace_Extender_XolPAP.stl](<../STL/HE Mounts/Xol_HE_Mount-Dragon-Ace_Extender_XolPAP.stl>) | UHF |
| Dragon Ace Volcano (with extender)<br/>`Use included 3mm spacer` | [Xol_HE_Mount-DragonUHF_Fan.stl](<../STL/HE Mounts/Xol_HE_Mount-DragonUHF_Fan.stl>) | [Xol_HE_Mount-DragonUHF_XolPAP.stl](<../STL/HE Mounts/Xol_HE_Mount-DragonUHF_XolPAP.stl>) | UHF |
| Dragon Ace Volcano (No extender)<br/>`Use included 3mm spacer`  | [Xol_HE_Mount-DragonUHF_Mini_Fan.stl](<../STL/HE Mounts/Xol_HE_Mount-DragonUHF_Mini_Fan.stl>) | [Xol_HE_Mount-DragonUHF_Mini_XolPAP.stl](<../STL/HE Mounts/Xol_HE_Mount-DragonUHF_Mini_XolPAP.stl>) | Standard |
| Revo Voron | [Xol_HE_Mount-Revo-Voron_Fan.stl](<../STL/HE Mounts/Xol_HE_Mount-Revo-Voron_Fan.stl>) | [Xol_HE_Mount-Revo-Voron_XolPAP.stl](<../STL/HE Mounts/Xol_HE_Mount-Revo-Voron_XolPAP.stl>) | Standard |
| NF-Crazy Volcano | [Xol_HE_Mount-NF-Crazy_Volcano_Fan.stl](<../STL/HE Mounts/Xol_HE_Mount-NF-Crazy_Volcano_Fan.stl>) | [Xol_HE_Mount-NF-Crazy_Volcano_XolPAP.stl](<../STL/HE Mounts/Xol_HE_Mount-NF-Crazy_Volcano_XolPAP.stl>) | UHF |

#### XolPAP Ducts
If you're using XolPAP remote cooling, you will need either standard or UHF length ducts:
* Standard: [XolPAP Standard Length Duct.stl](<../STL/XolPAP ducts/XolPAP Standard Length Duct.stl>)
* UHF: [XolPAP UHF Length Duct.stl](<../STL/XolPAP ducts/XolPAP UHF Length Duct.stl>)

`⚠️ * G2SA and WWG2 extruders not compatible with XolPAP `

### Extruder Mount

Pick one extruder mount from the table below to match your extruder, and if it's going on Xol-Carriage or on TAP/Voron carriage.

| Extruder | Xol-Carriage | TAP / Voron Carriage |
| --- | --- | --- |
| Sherpa-Mini / <br/> Sharkfin  <br/>`K-face plate and optional` <br/> `short idler arm for Sherpa-Mini ` <br/> `from Annex Engineering`<br/> [Sherpa front k-face](<https://github.com/Annex-Engineering/Sherpa_Mini-Extruder/blob/master/STLs/optional_parts/%5Ba%5D_housing_front_k_x1_rev15.STL>) <br/> [Sherpa short idler arm](<https://github.com/Annex-Engineering/Sherpa_Mini-Extruder/blob/master/STLs/optional_parts/%5Ba%5D_idler_arm_short_x1_rev16a.STL>) | [Xol Extruder Mount - Sherpa-Mini.3mf](<../STL/Extruder Mounts/Xol Extruder Mount - Sherpa-Mini.3mf>) | [Xol Extruder Mount - Sherpa Mini - TAP.3mf](<../STL/Extruder Mounts/Xol Extruder Mount - Sherpa Mini - TAP.3mf>) |
| Annex Double Folded Ascender | [Xol Extruder Mount - DFA.stl](<../STL/Extruder Mounts/Xol Extruder Mount - DFA.stl>) <br/> *License [Note](<DFA_MOD_License.md>) | Not Supported |
| Vz-Hextrudort-Low / <br/> LGX-Lite | [Xol Extruder Mount - VZ-Hex+LGX-L.stl](<../STL/Extruder Mounts/Xol Extruder Mount - VZ-Hex+LGX-L.stl>) | [Xol Extruder Mount - VZ-Hex+LGX-L - TAP.stl](<../STL/Extruder Mounts/Xol Extruder Mount - VZ-Hex+LGX-L - TAP.stl>) |
| Galileo G2SA (Orbiter mount pattern) <br/> `NOT XolPAP Compatible` | [Xol Extruder Mount - G2SA.stl](<../STL/Extruder Mounts/Xol Extruder Mount - G2SA.stl>), AND <br/>  [G2SA front for Xol Extruder Mount.stl](<../STL/Extruder Mounts/G2SA front for Xol Extruder Mount.stl>) | [Xol Extruder Mount - G2SA - TAP.stl](<../STL/Extruder Mounts/Xol Extruder Mount - G2SA - TAP.stl>) , AND <br/>  [G2SA front for Xol Extruder Mount.stl](<../STL/Extruder Mounts/G2SA front for Xol Extruder Mount.stl>) |
| WristWatch G2 (Orbiter mount pattern)  <br/> `NOT XolPAP Compatible` | [Xol Extruder Mount - G2SA.stl](<../STL/Extruder Mounts/Xol Extruder Mount - G2SA.stl>), AND <br/>  [WWG2 front for Xol Extruder Mount.stl](<../STL/Extruder Mounts/WWG2 front for Xol Extruder Mount.stl>) | [Xol Extruder Mount - G2SA - TAP.stl](<../STL/Extruder Mounts/Xol Extruder Mount - G2SA - TAP.stl>) , AND <br/>  [WWG2 front for Xol Extruder Mount.stl](<../STL/Extruder Mounts/WWG2 front for Xol Extruder Mount.stl>) |
| WristWatch BMG | [Xol Extruder Mount - G2SA.stl](<../STL/Extruder Mounts/Xol Extruder Mount - G2SA.stl>), AND <br/>  [WWBMG front for Xol Extruder Mount.stl](<../STL/Extruder Mounts/WWBMG front for Xol Extruder Mount.stl>) | [Xol Extruder Mount - G2SA - TAP.stl](<../STL/Extruder Mounts/Xol Extruder Mount - G2SA - TAP.stl>) , AND <br/>  [WWBMG front for Xol Extruder Mount.stl](<../STL/Extruder Mounts/WWBMG front for Xol Extruder Mount.stl>) |
| Escapement | [Xol Extruder Mount - Escapement.stl](<../STL/Extruder Mounts/Xol Extruder Mount - Escapement.stl>) | [Xol Extruder Mount - Escapement - TAP.stl](<../STL/Extruder Mounts/Xol Extruder Mount - Escapement - TAP.stl>) |
| Orbiter v2.0 | [Xol Extruder Mount - Orbiter V2.stl](<../STL/Extruder Mounts/Xol Extruder Mount - Orbiter V2.stl>) | [Xol Extruder Mount - Orbiter V2 - TAP.stl](<../STL/Extruder Mounts/Xol Extruder Mount - Orbiter V2 - TAP.stl>) |

 ### Faceplate
There's only one option for the faceplate now. If you don't want an LED in the status light area, print the "diffuser" in a contrasting colour to the main faceplate part to show off the Xol logo.
* [Faceplate.stl](../STL/Faceplate/Faceplate.stl)
* [[t] Logo LED diffuser.stl](<../STL/Faceplate/[t] Logo LED diffuser.stl>) `Clear/translucent for diffuser, or contrasting colour for no LED`

 #### EBB 36 Mount
 Print the EBB 36 mount for Xol-Carriage to suit your CAN or break-out board / extruder combination.<br/>
 `If you aren't using Xol-Carriage (TAP users) there are numerous EBB mounts availble like these from KayosMaker:`[CANboard_Mounts](https://github.com/KayosMaker/CANboard_Mounts)
| Extruder | Without strain relief | With strain relief|
|-----|---|---|
|Sherpa-Mini |[EBB36 Mount - Sherpa-Mini.stl](<../STL/EBB Mounts/EBB36 Mount - Sherpa-Mini.stl>)|[EBB36 Mount - Sherpa-Mini [strain relief].stl](<../STL/EBB Mounts/EBB36 Mount - Sherpa-Mini [strain relief].stl>) |
|WW-BMG |[EBB36 Mount - WWBMG.stl](<../STL/EBB Mounts/EBB36 Mount - WWBMG.stl>)|[EBB36 Mount -WWBMG [strain relief].stl](<../STL/EBB Mounts/EBB36 Mount -WWBMG [strain relief].stl>)
|DFA | {todo} | {todo} |
| Galileo 2SA | {todo} | {todo} |
| Escapement | {todo} | {todo} |
|VZ-Hextrudort-Low | [EBB36 Mount - VZ-Hextrudort-Low.stl](<../STL/EBB Mounts/EBB36 Mount - VZ-Hextrudort-Low.stl>) | [EBB36 Mount - VZ-Hextrudort-Low [strain relief].stl](<../STL/EBB Mounts/EBB36 Mount - VZ-Hextrudort-Low [strain relief].stl>) |
| LGX-Lite | {todo} | {todo} |
|Orbiter v2.0 | [EBB36 Mount - Orbiter2.0.stl](<../STL/EBB Mounts/EBB36 Mount - Orbiter2.0.stl>) | [EBB36 Mount - Orbiter2.0 [strain relief].stl](<../STL/EBB Mounts/EBB36 Mount - Orbiter2.0 [strain relief].stl>) |

### M2.5 Savers
 Add a little colour, and protect your delicate 4010 blower fans <br/>
* [[a]_M2.5_saver_x4.stl](../STL/Faceplate/[a]_M2.5_saver_x4.stl) `These aren't optional extras, you need them to protect your fans. Also the screw holes are too shalow without them`

### Trident stepper spacer
On some Trident printers, the leadscrews are slightly too high and may collide with the Xol ducts when the toolhead is at the very front corners of the printer (usually only the right side when homing at Y,0). <br/>
To avoid this colision, there is a spacer available on printables that will lower the leadscrew stepper motors: [https://www.printables.com/model/486638-voron-trident-z-steppers-spacers](https://www.printables.com/model/486638-voron-trident-z-steppers-spacers)

<br/><br/><br/><br/>

⬅ [BOM](BOM.md) - [Carriage assembly](xol_carriage_assembly.md) ➡

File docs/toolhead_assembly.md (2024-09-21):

# Xol Toolhead Assembly



`The details below are for Rapido and Sherpa-Mini. We have faith that you can work it out from here if you're using a different combination of hotend and extruder. If you have trouble look for the #xol-toolhead channel on the Discord.`
|	Notes	|	Image	|
|	---	|	---	|
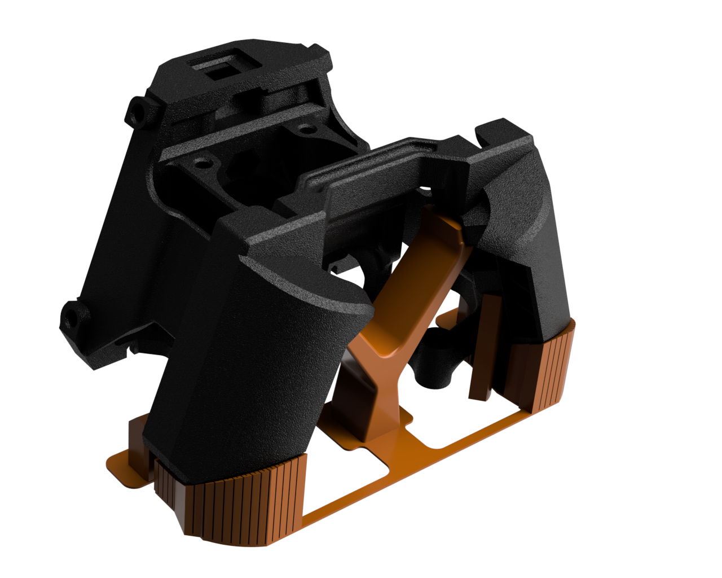
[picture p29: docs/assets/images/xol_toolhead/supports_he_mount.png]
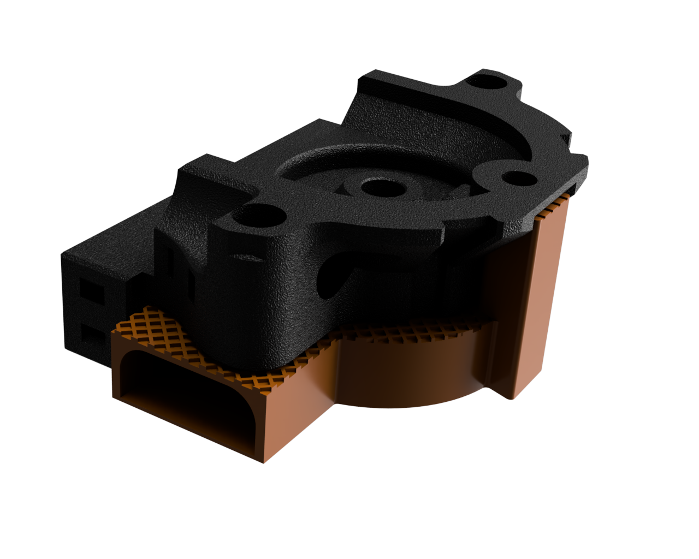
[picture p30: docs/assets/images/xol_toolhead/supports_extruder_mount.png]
|	Remove the included supports. They're going to get in the way if you don’t.	|		|
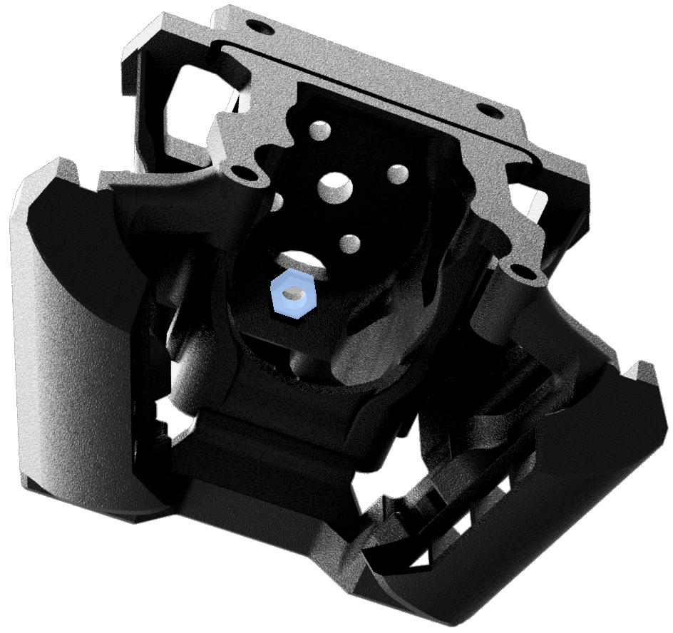
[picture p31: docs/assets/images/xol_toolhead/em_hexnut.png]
|	An easy one to start, put one M3 hexnut into the hotend mount. <br/>`Pushes in from below on most, slides in from the side for NF-Crazy & XG`	|		|
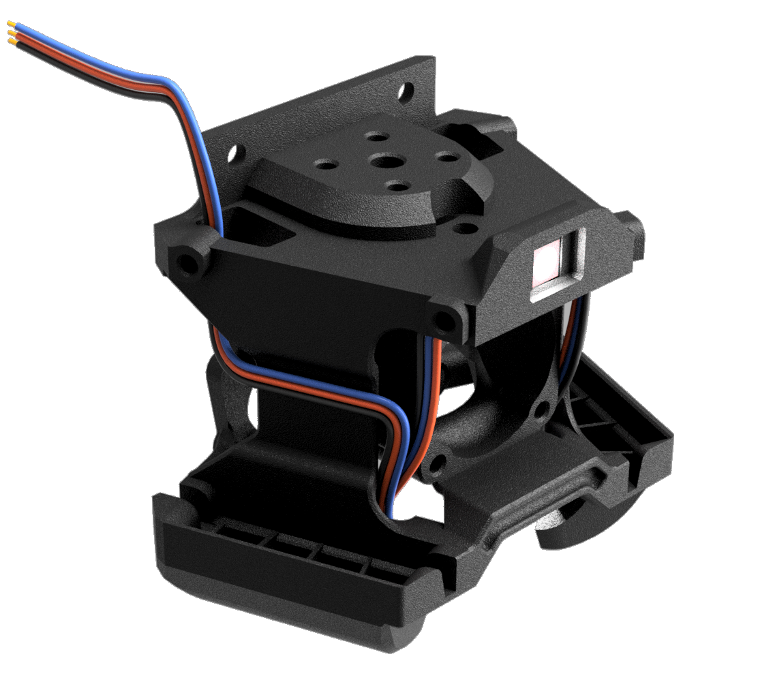
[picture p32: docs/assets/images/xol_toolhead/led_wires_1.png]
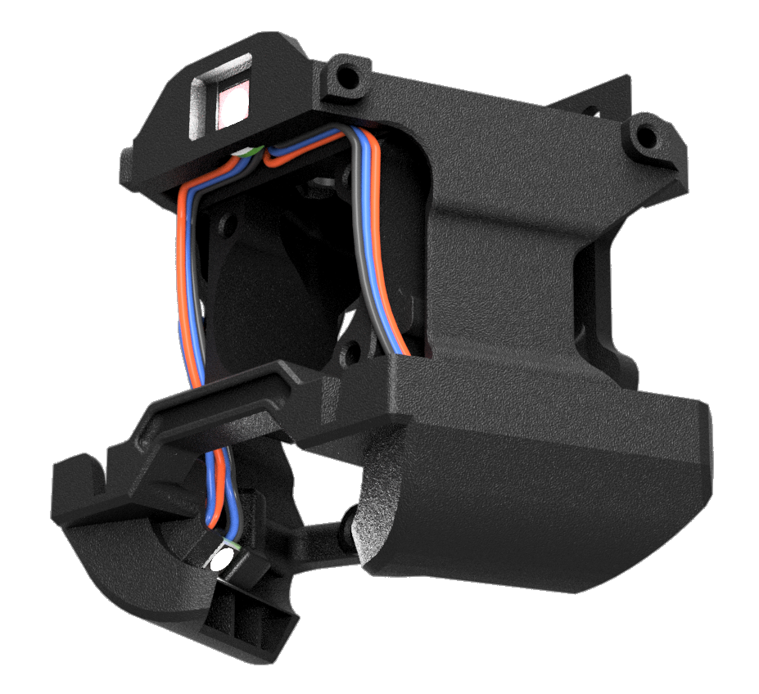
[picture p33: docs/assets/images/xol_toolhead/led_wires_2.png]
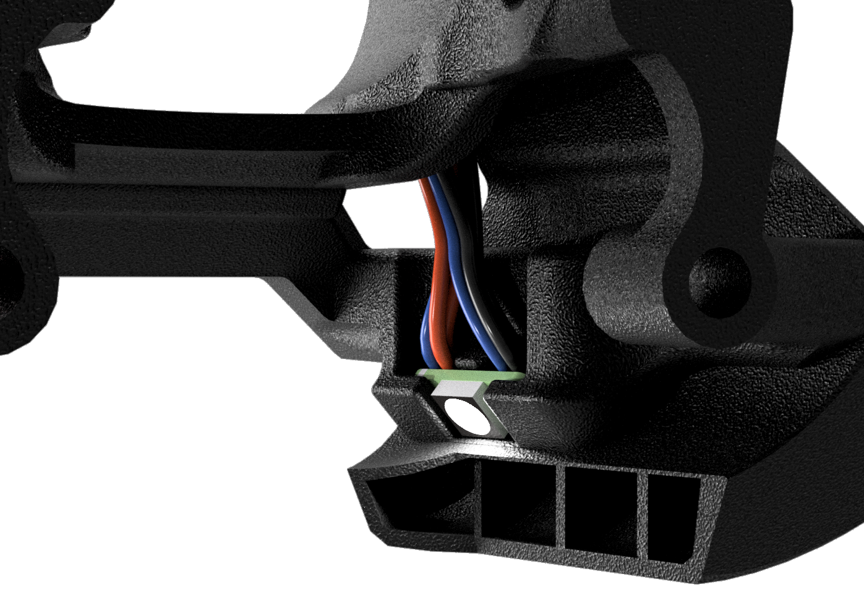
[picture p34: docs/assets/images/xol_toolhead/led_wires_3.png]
|	LEDs are next (if you're using them). <br/>Push them into the slots provided. <br/><br/> Build instructions for the LED harness can be found [here](led_harness.md)	|	<br/><br/>	|
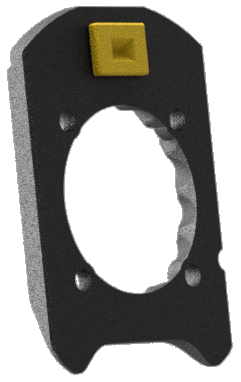
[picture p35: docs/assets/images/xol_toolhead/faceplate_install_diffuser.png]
|	Push the diffuser (or accent logo piece) into the faceplate.	|		|
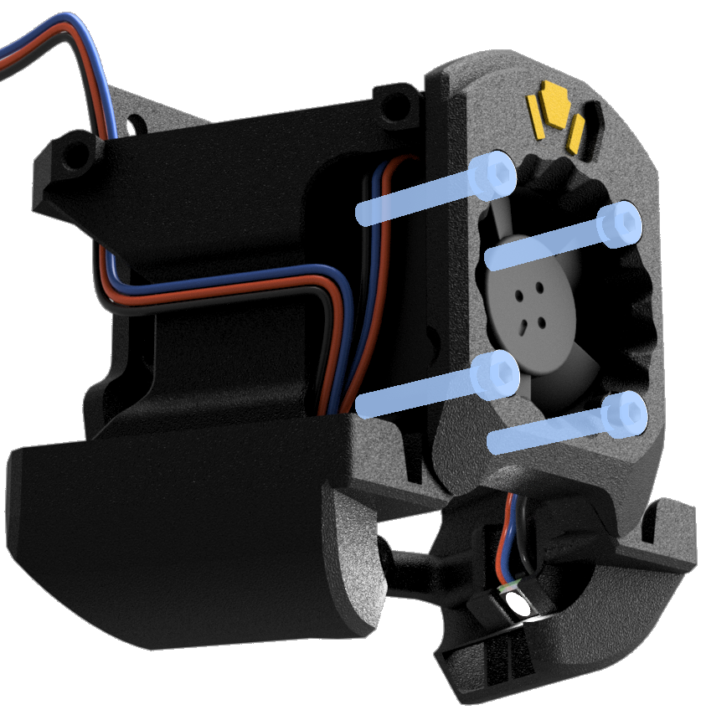
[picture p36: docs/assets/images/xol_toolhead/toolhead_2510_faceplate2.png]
|	Install the 2510 hotend fan. Make sure you don't squash any LED wires, and secure with <br/>4x M2.5x16 SHCS.<br/><br/>⚠️ **Screws are going into plastic. Do NOT over tighten** <br/><br/>`If you want a version with heatset inserts, there is a mod here:`<br/>[Heatsets_Xol_HE_Mount](https://github.com/Armchair-Heavy-Industries/Armchair-Usermods/tree/main/files/Xol-Toolhead/Heatset_Xol_HE_Mount) |		|
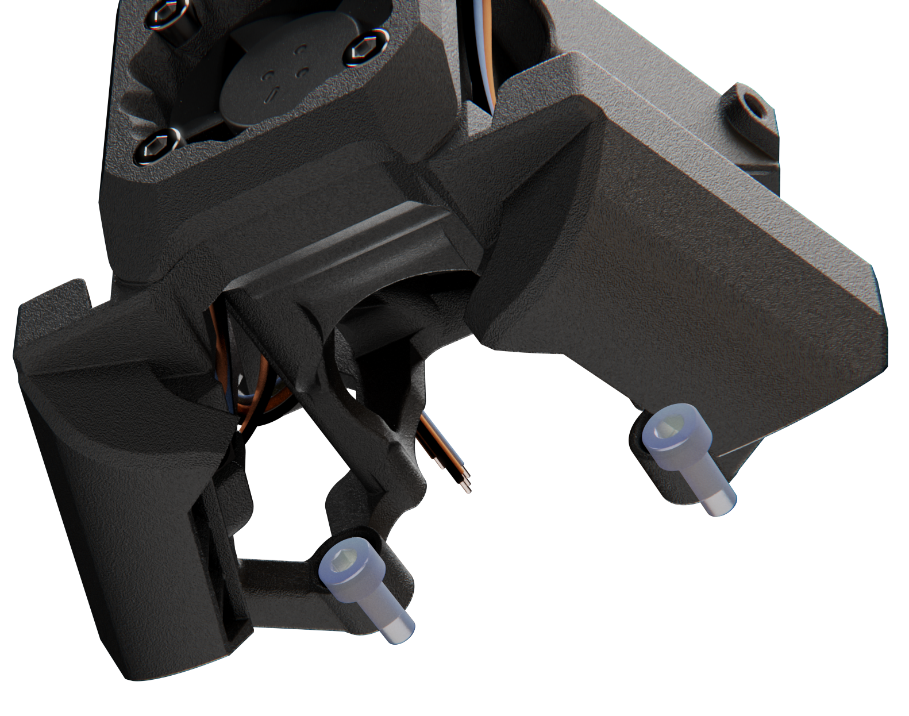
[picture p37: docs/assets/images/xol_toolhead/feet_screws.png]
|	Put the screws into the "feet" now, your hotend may be in the way later.<br/>2x M3x8 SHCS	|		|
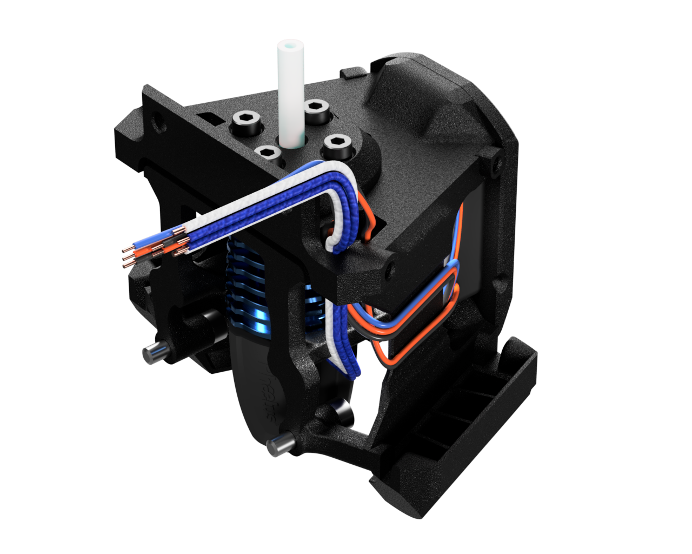
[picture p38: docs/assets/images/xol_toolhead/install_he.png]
|	Install your hotend into the mount. Don't forget the PTFE tube. |		|
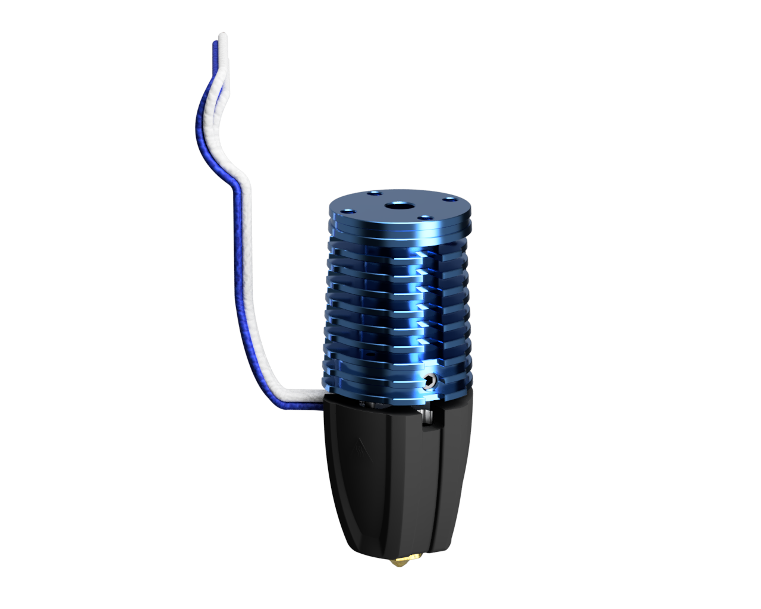
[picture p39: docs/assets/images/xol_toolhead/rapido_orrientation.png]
|	⚠️ **If installing Rapido, you will need to make sure that it has the correct alignment.** <br/>You should see the grub screw in the heat sink slightly to the right of center when the wires are coming out to the left side.	|		|
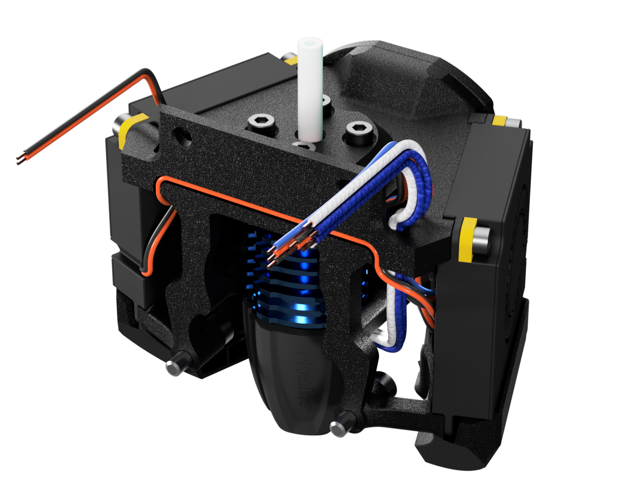
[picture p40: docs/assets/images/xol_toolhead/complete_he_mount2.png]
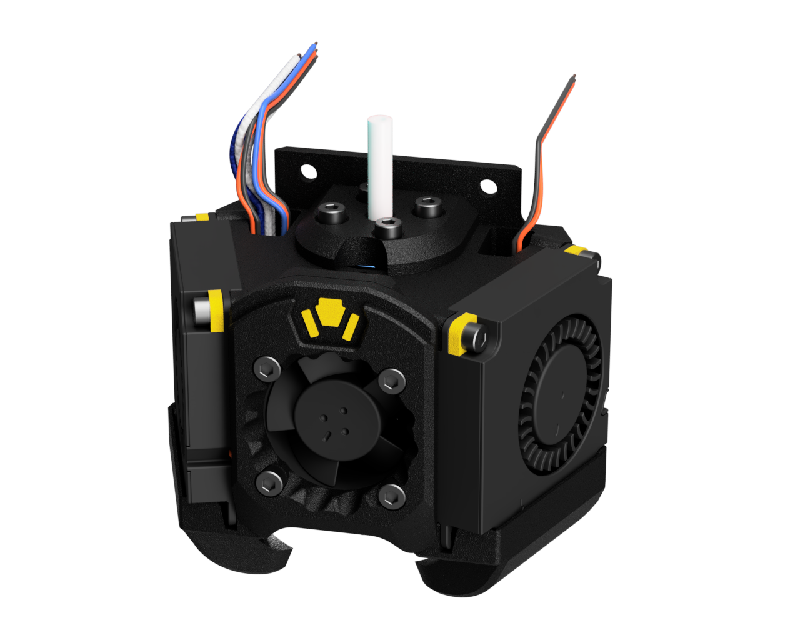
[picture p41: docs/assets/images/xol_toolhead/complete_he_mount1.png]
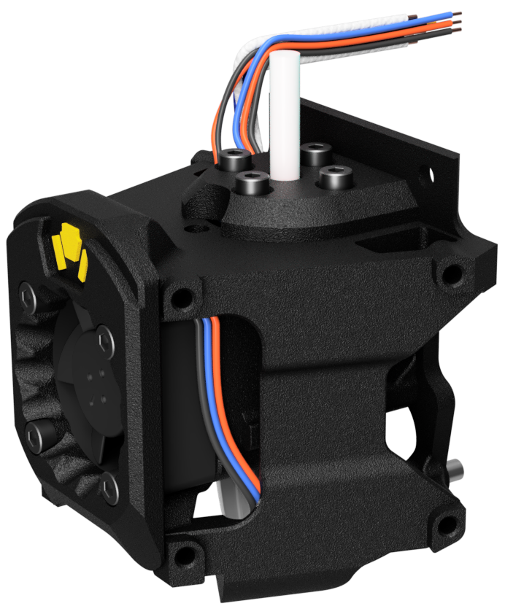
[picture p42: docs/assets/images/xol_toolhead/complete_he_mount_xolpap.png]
|	Slide the fans in and fix with printed parts and screws. `The printed parts protect the 4010 blower mounting ears. Don't skip them`<br/>4x M2.5 saver [printed part]<br/>4x M2.5x8 SCHS<br/><br/>⚠️ **Screws are going into plastic. Do NOT over tighten**<br/><br/>[Heatsets mod](https://github.com/Armchair-Heavy-Industries/Armchair-Usermods/tree/main/files/Xol-Toolhead/Heatset_Xol_HE_Mount)<br/><br/><br/><br/>XolPAP users can skip this step. Those ducts are put on at the end.	|	<br/>	|
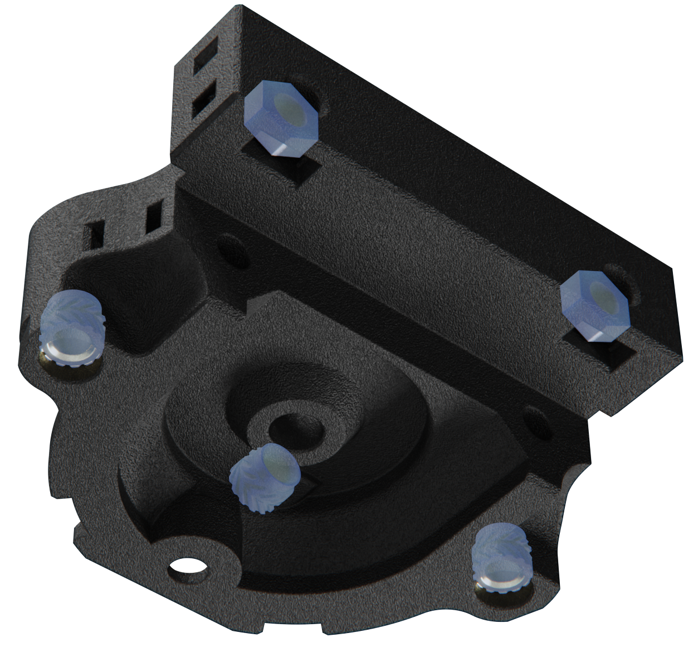
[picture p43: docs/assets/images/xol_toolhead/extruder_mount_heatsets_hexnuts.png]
|	Time to move onto the extruder mount assembly. Install 2 or 3 heatset inserts and 2 hex nuts into your extruder mount.	|		|
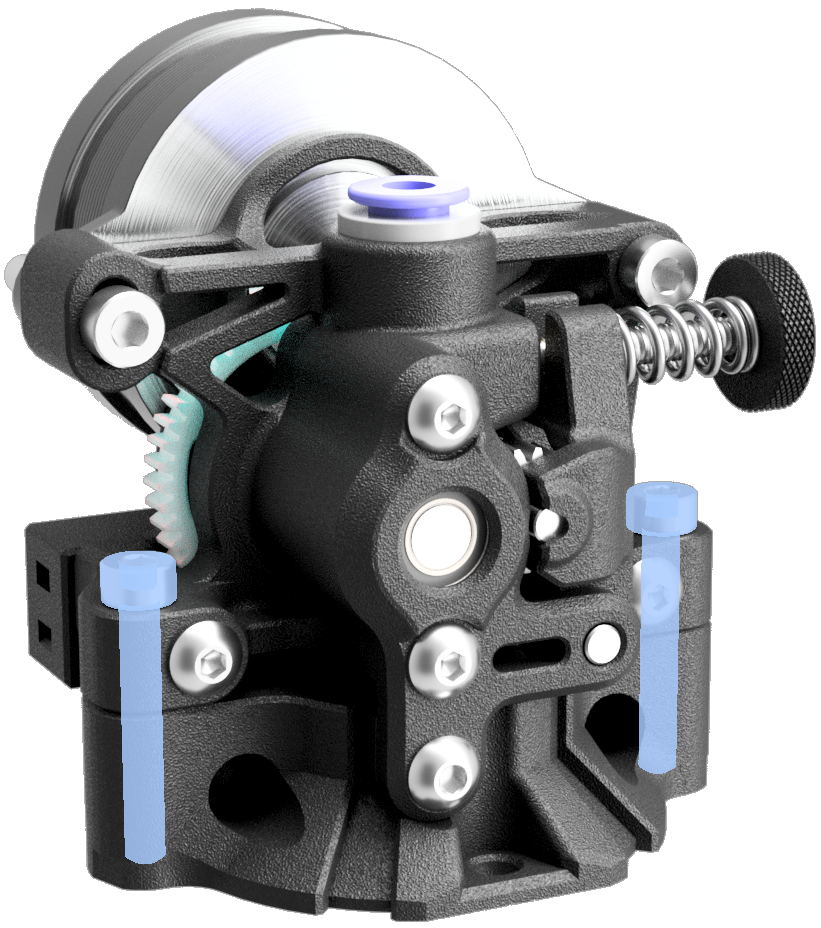
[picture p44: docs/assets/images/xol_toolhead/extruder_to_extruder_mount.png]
|	Attach the extruder to the extruder mount.<br/>2x M3x20 SHCS for Sherpa-Mini (usually M3x8 SHCS for others)<br/>1x M3x6 BHCS for extruder faceplate where applicable.	|		|
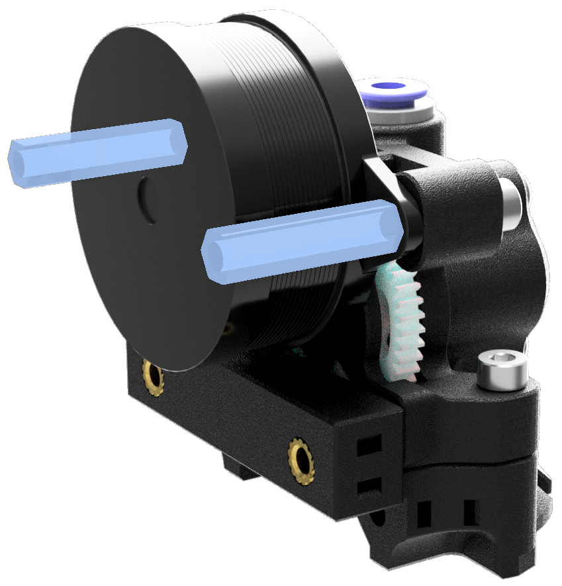
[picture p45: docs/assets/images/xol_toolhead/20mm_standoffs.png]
|	Screw your 20mm stand-offs onto the long screws you used to attach your extruders stepper motor.	|		|
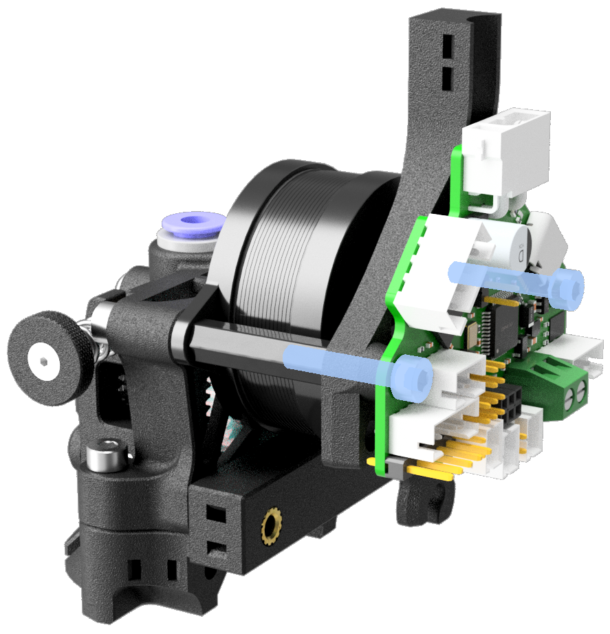
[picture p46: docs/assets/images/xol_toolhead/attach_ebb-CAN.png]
|	Now you can mount your toolhead board/CAN board/strain relief printed part etc. to the stand-offs<br/>2x M3x16 SHCS	|		|
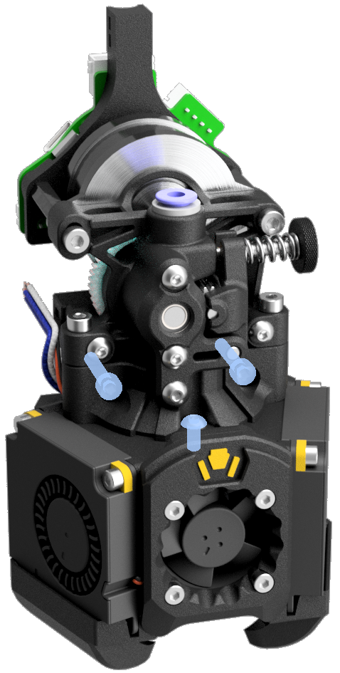
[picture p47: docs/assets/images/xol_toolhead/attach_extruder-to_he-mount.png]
|	The extruder assembly is now combined with the HE mount assembly.<br/>1x M3x6 BHCS<br/>2x M3x16 SHCS `Just through enough to hold it all together`	|		|
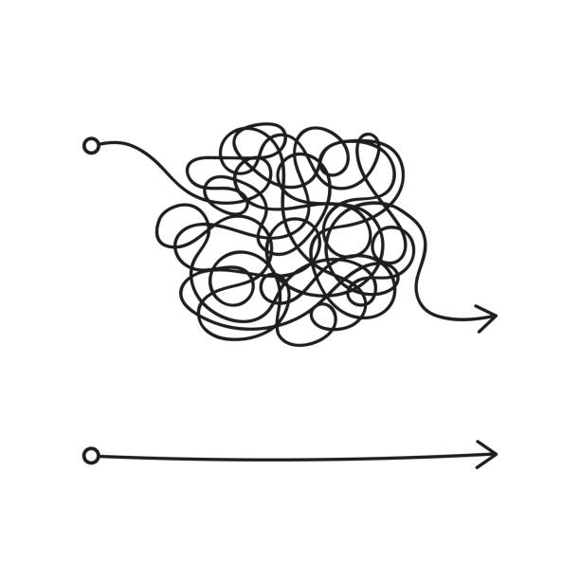
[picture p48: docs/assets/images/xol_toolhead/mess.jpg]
|	Now that everything is together, those using CAN or other toolhead boards can cut/crimp/tidy wiring to the right lengths before final assembly.	|		|
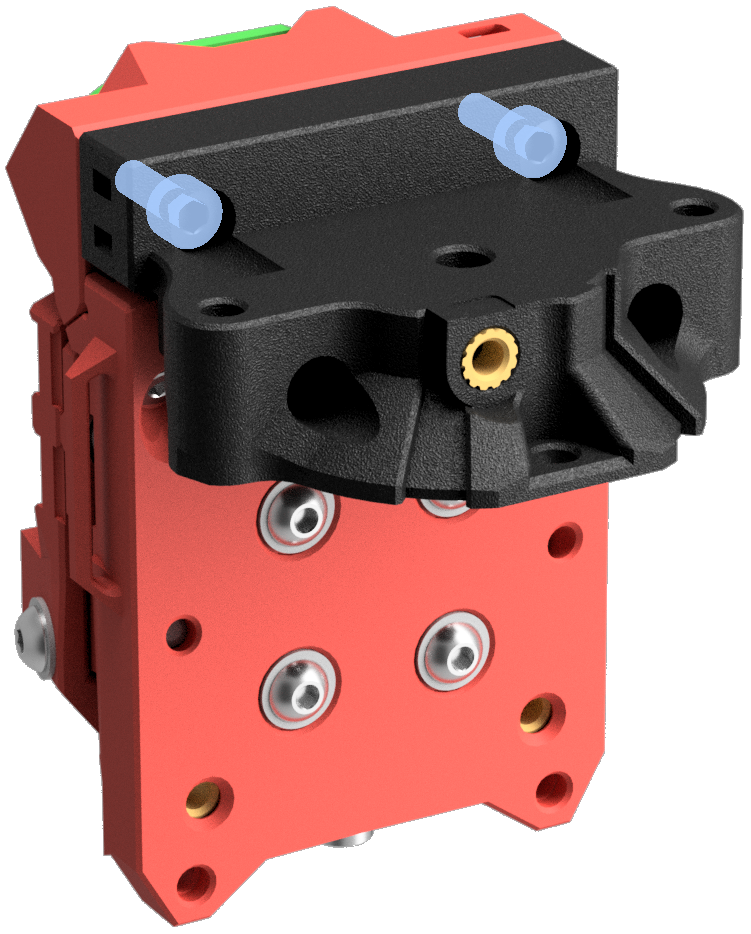
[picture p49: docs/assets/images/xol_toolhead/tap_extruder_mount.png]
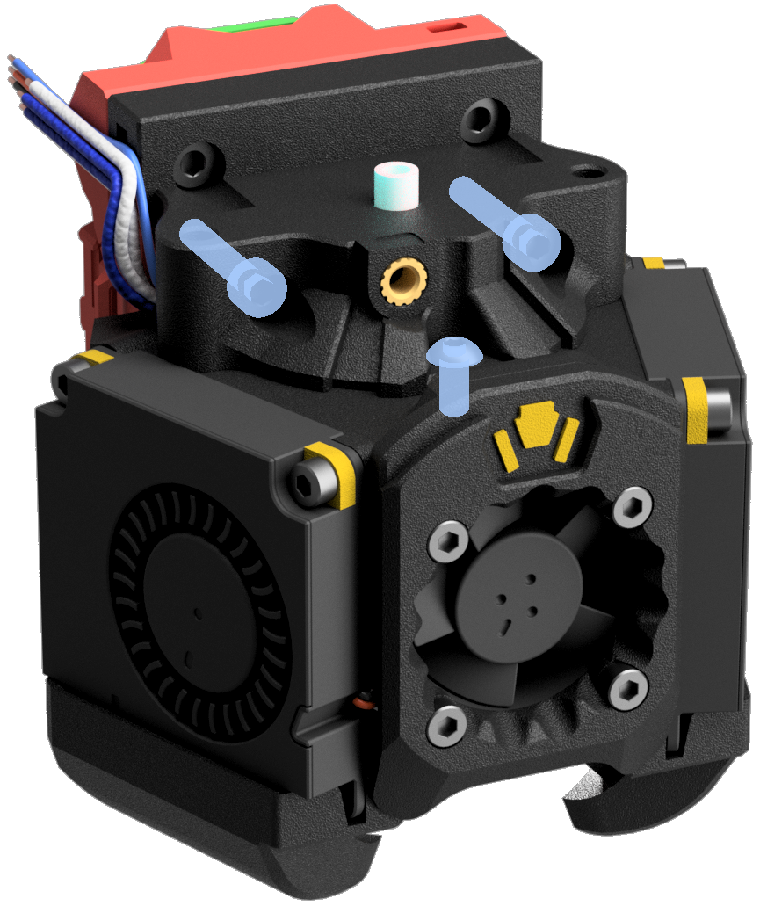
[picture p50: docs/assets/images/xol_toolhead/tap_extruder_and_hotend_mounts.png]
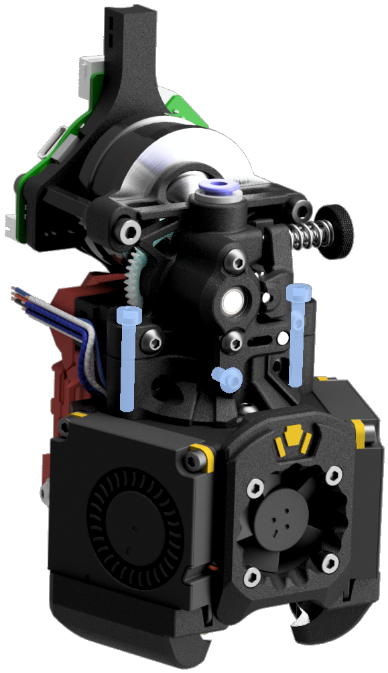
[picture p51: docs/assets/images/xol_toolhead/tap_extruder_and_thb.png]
|	⚠️ **Tap/Standard Voron carriage users only!**<br/><br/>Now you have to undo your cables from your toolhead board and pull the extruder assembly off again.<br/><br/>Take the extruder off the extruder mount, and attach it to the top of the Tap/Voron carriage with 2x M3x8 SHCS.<br/><br/>Slide the HE mount assembly up under the extruder mount and re-attach the HE mount to the extruder mount.⚠️ `Rember you're probably screwing into plastic on a Voron carriage here!`<br/><br/>Now you can put your extruder/toolhead board bits back on and reconnect all your wires.	|	<br/><br/>	|
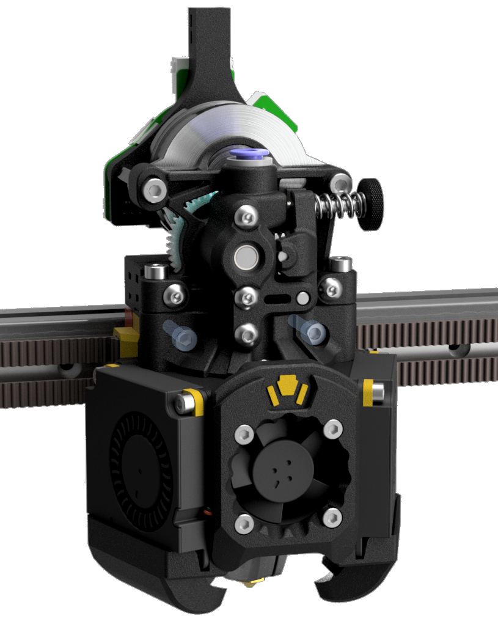
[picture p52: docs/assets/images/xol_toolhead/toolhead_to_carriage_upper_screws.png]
|	Now that we have that Tap stuff out of the way. Time to get things attached for Xol Carriage.<br/><br/>Start with the two front, upper screws<br/>2x M3x16 that were already there but need to be tightened.<br/><br/>⚠️ **Do NOT over tighten.**	|		|
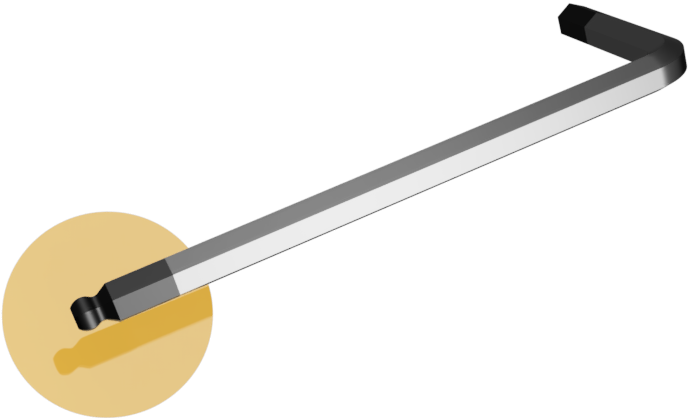
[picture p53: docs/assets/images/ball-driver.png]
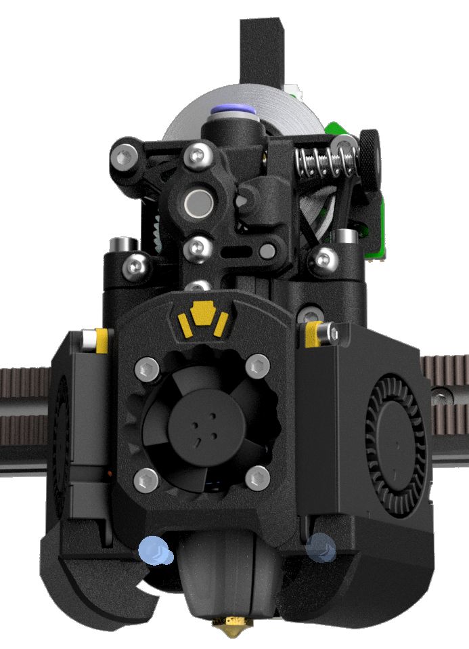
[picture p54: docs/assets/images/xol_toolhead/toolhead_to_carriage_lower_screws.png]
|	⚠️ **The front lower screws need a ball head hex driver. Don't strip your SHCS.**<br/><br/>Tighten the feet<br/>2x M3x8 SHCS, that were also already there. <br/><br/>`This is for Tap/Voron Carriages too.`	|		|
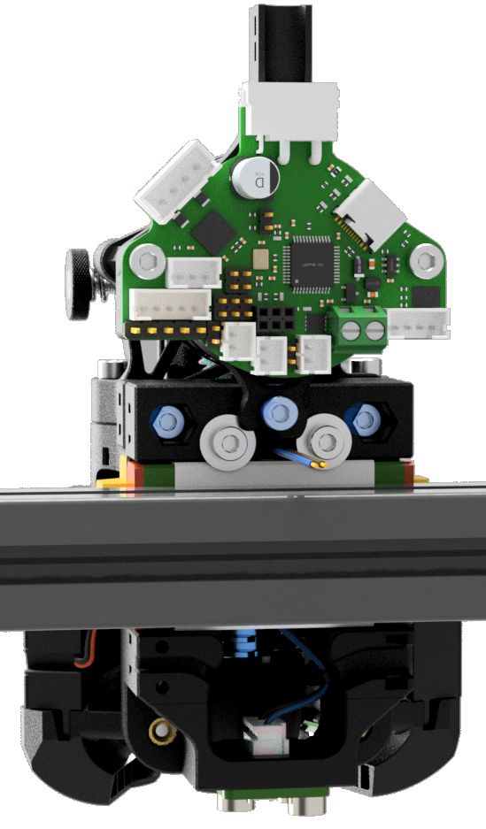
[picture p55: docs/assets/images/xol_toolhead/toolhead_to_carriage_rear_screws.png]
|	Reach around the back for the last 3 screws!<br>3x M3x8 SHCS <br/><br/>`Sorry XolPAP users, you have some more screws`<br/><br/>`Don't forget to connect your probe`	|		|
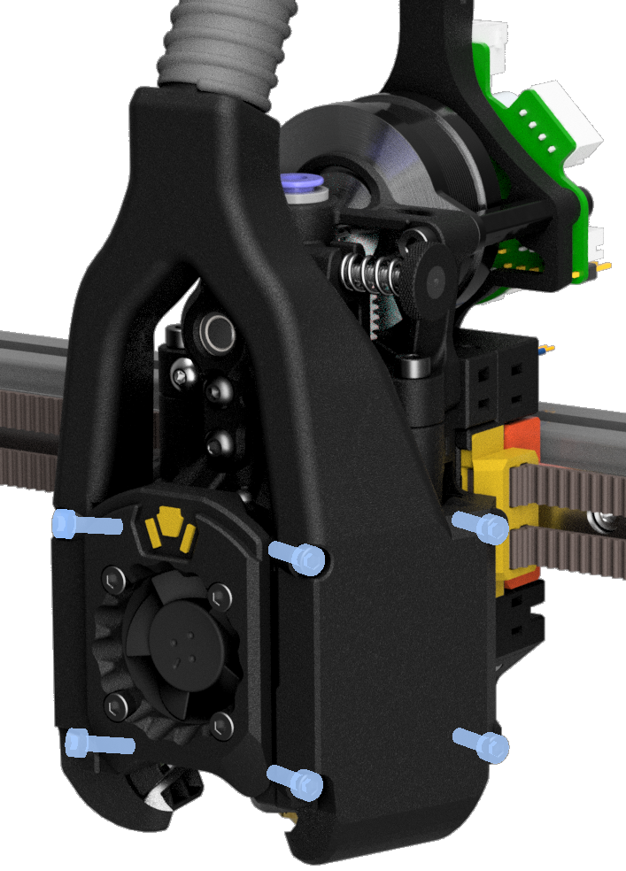
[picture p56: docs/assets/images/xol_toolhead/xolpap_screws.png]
|	Alright XolPAP fans, we're finally here. Slide the ducts over the toolhead and attach with<br/>8x M2.5x8 SHCS `4 per side`<br/><br/>⚠️ **Screws are going into plastic. Do NOT over tighten**<br/>[Heatsets mod](https://github.com/Armchair-Heavy-Industries/Armchair-Usermods/tree/main/files/Xol-Toolhead/Heatset_Xol_HE_Mount)	|		|
|Don't forget your software configuration!| ⚠️ Things are probably different with your new setup. <br/> <br/> * Endstop positions for X: `[stepper_x]` check `position_endstop` and `position_max` <br/> * Your probe offset: Do a `probe_calibrate` <br/> You know your printer better than anyone else. Check your work. |

<br/><br/><br/><br/>
 ⬅ [Carriage assembly](xol_carriage_assembly.md) - [LED Harness instructions](led_harness.md) ➡

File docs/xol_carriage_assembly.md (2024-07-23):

# Xol Carriage Assembly
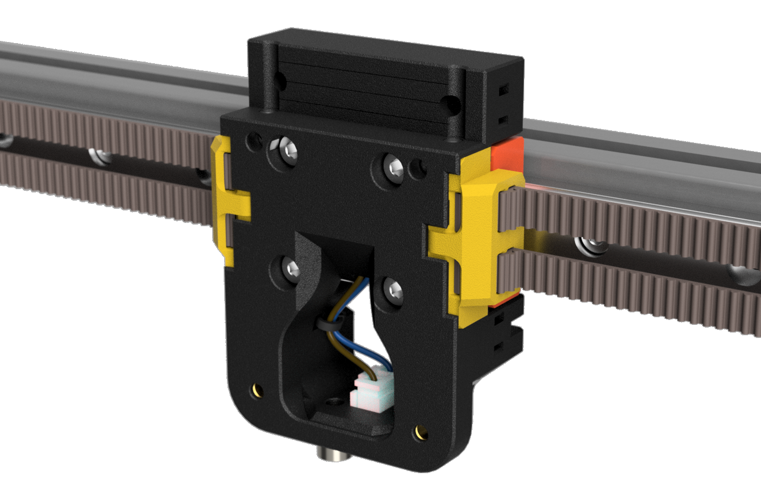
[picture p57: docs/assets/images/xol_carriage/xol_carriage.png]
Xol Carriage Image


| Notes | Image |
| --- | --- |
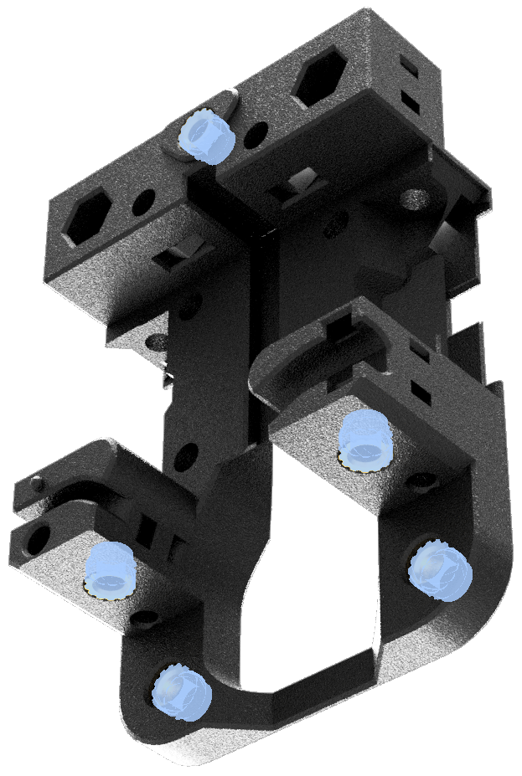
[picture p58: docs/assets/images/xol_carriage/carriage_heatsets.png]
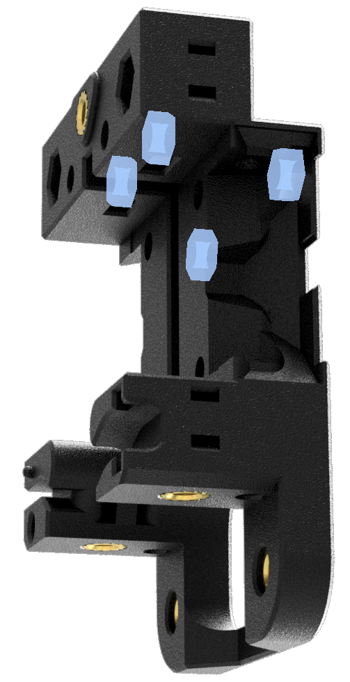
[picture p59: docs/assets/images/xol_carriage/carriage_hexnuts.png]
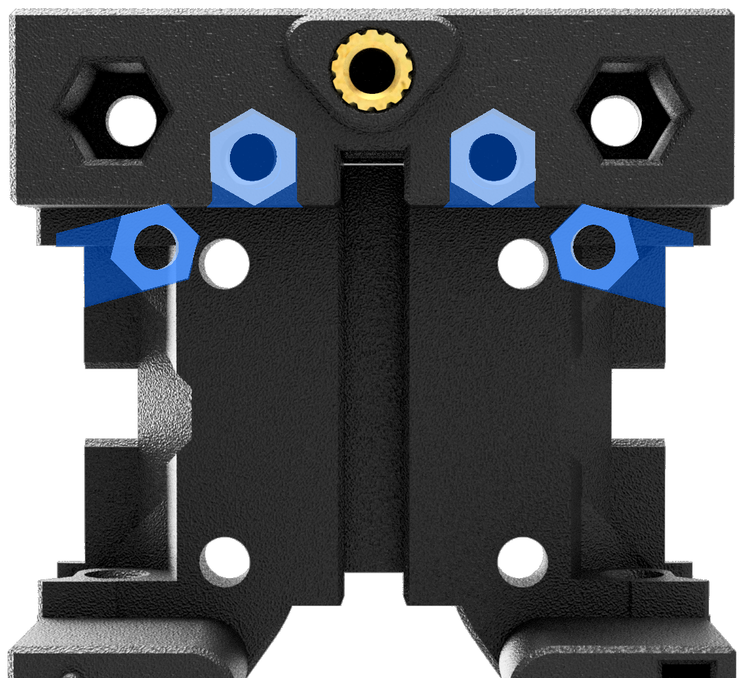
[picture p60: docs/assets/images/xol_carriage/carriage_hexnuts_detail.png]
| Get the carriage ready by installing <br /> * 5x M3 heatsets<br />* 4x M3 hex nuts |  <br/>  <br/>  |
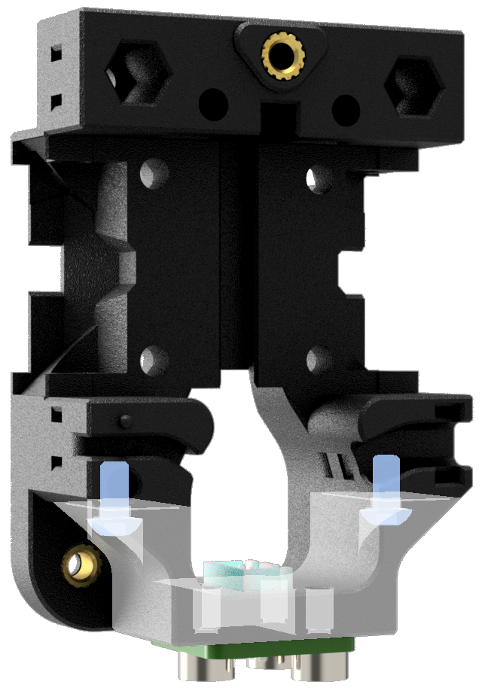
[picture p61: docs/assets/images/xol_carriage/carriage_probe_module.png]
| Attach your probe module with 2x M3x6 BHCS |  |
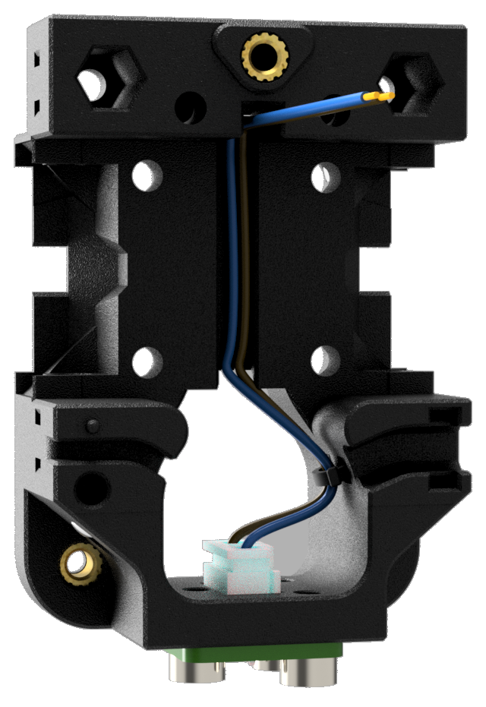
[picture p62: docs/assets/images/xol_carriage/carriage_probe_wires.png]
| Run the probe wires up the channel before you install the carriage on the MGN rail. Don't forget to keep them secure using the cable tie slots. |  |
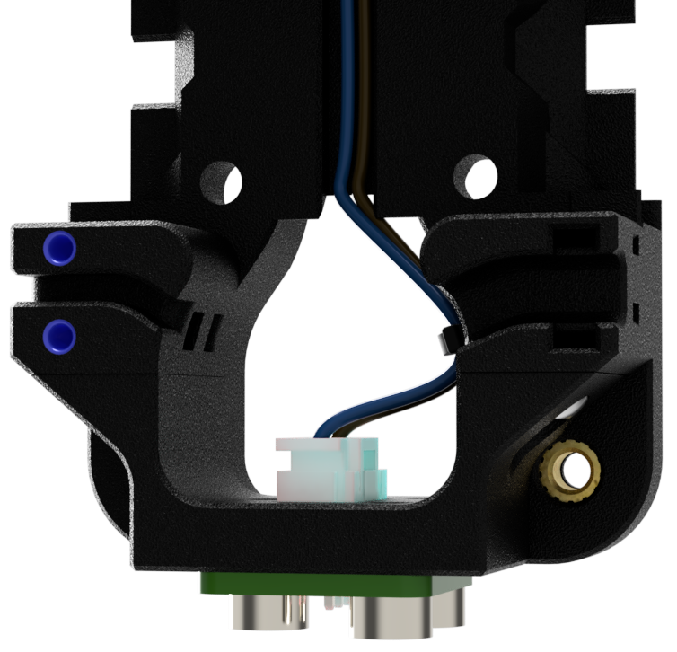
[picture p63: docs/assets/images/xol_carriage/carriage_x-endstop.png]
| `Option`<br/>_*If you haven't yet converted to sensorless homing, your X-endstop switch can be attached to the back of the carriage._<br/><br/> Install the switch with 2x M2x10 self tapping screws |  |
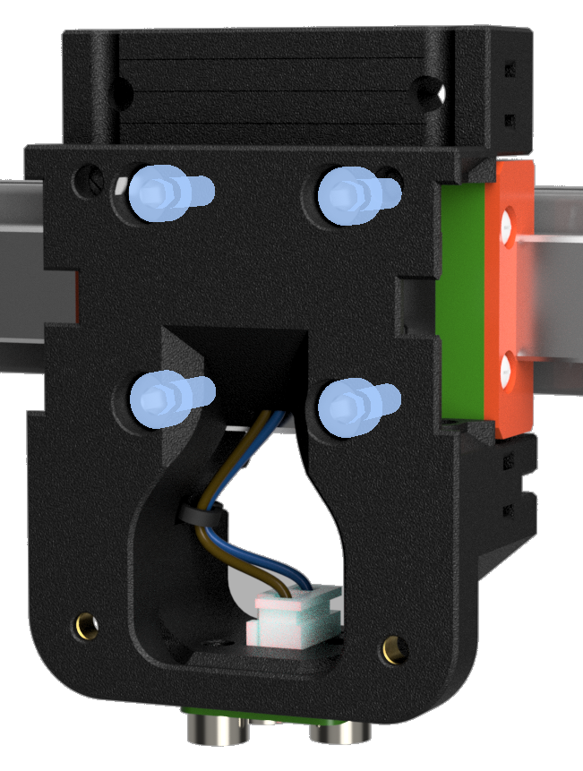
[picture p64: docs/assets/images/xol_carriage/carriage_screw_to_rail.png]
| Put the carriage on the MGN rail with <br />4 M3x8 SHCS<br/> |  |
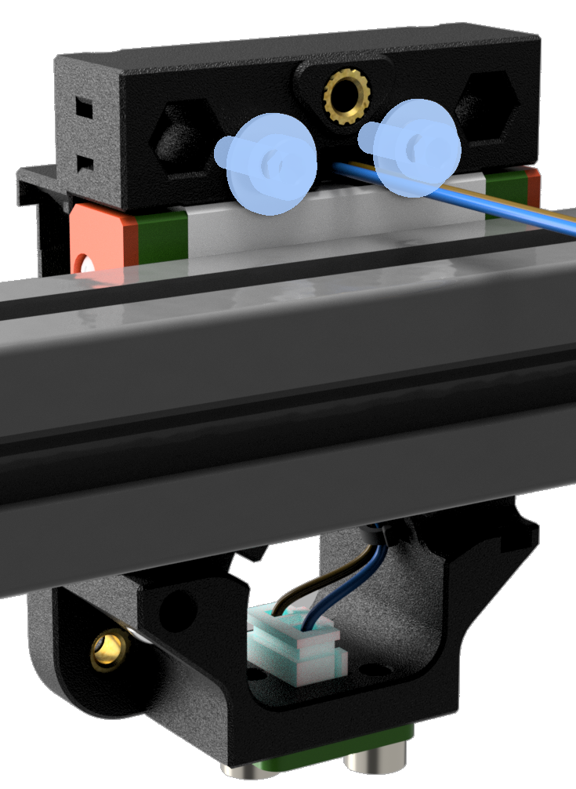
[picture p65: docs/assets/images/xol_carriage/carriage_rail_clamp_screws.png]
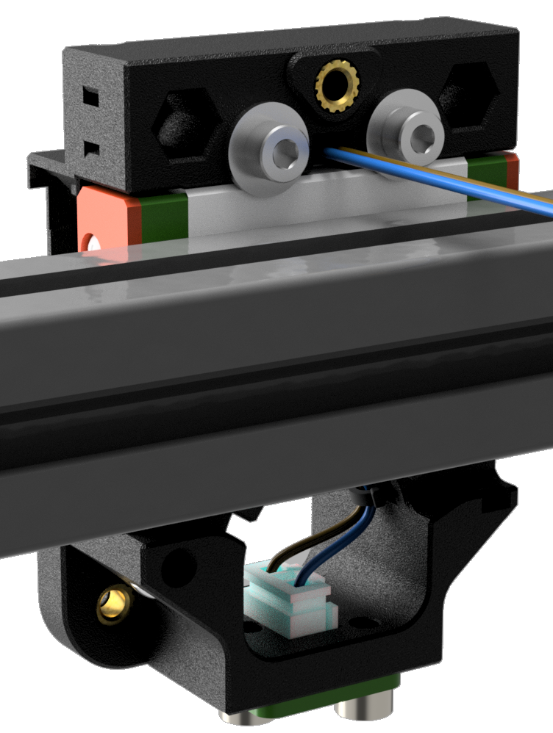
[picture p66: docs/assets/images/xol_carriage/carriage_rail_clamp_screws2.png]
| Use 2x M3x8 SHCS and 2x large M3 washers to 'clamp' the carriage to the MGN rail. `M3 + M5 washers can be stacked if you don't have the large M3 washers` |  <br/>  |
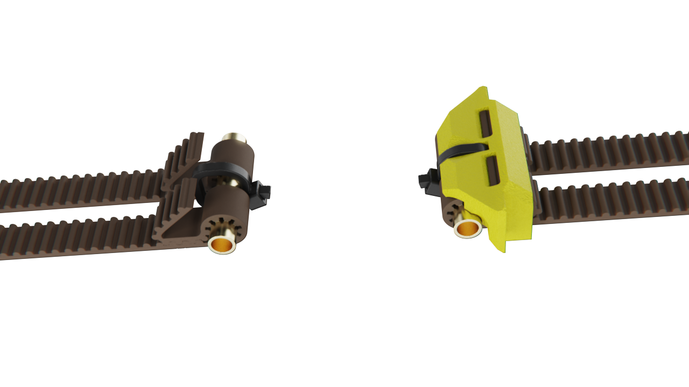
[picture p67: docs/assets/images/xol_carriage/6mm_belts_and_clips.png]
| Install the belts and tubes into the belt clips. It should look like the picture when installed correctly.<br/> `Left clip hidden to show the belt path inside the clip` <br/> <br/>  * Pull your belt through the belt clips.<br/>  * Make a loop and pinch together so that the teeth are locking together.<br/>  * Pull the belt back through the same hole in the clip.<br/>  * Repeat for the 2nd belt, leaving enough slack so you can slide the 4mm OD tube through the opening of the loops. <br/> * Pull the belts tight around the tube.<br/> * Use a small cable tie, or wire tie to pull the tube into the recess in the clip and hold it tight in position.<br/> * Tuck the excess belt back into the clip. |  |
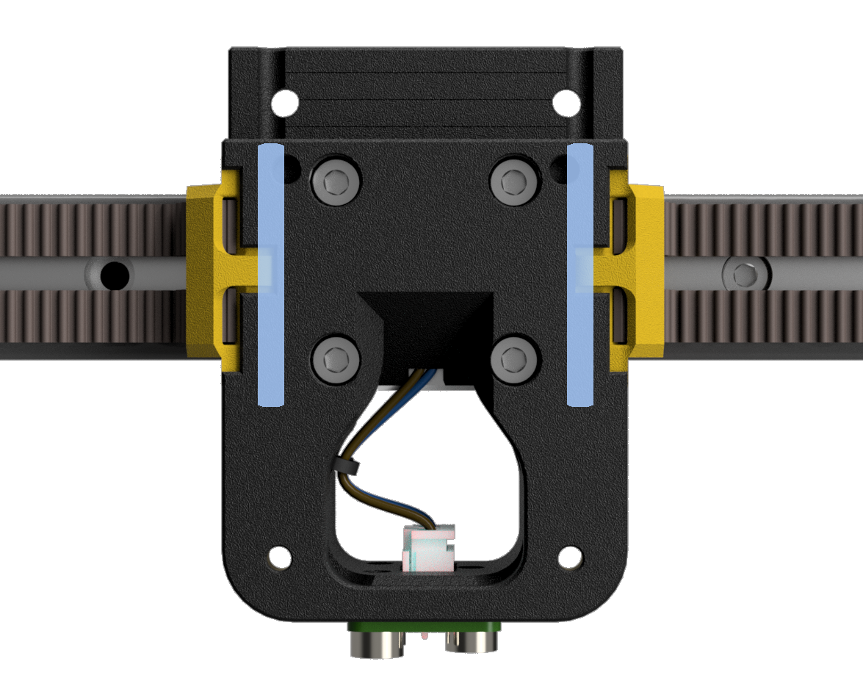
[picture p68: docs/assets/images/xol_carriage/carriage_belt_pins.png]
| Push the belt/clip/tube assembly into the side of the carriage so that it lines up and you can push the M3x30 pin down from the top and through the tube. Repeat for the other side. |  |
| Tada!!! You have a completed Xol Carriage ready to attach the toolhead |  |

<br/><br/><br/><br/>
⬅  [Printed parts](printing.md) - [Toolhead assembly](toolhead_assembly.md) ➡

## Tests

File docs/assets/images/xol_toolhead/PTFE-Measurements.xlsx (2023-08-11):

Hotend | Depth
Rapido | 15
Dragon | 1
Dragon UHF | 0
XG | 1
NeXt-G | 1
K1 | 1
Revo Voron | 7.35
Extruder | Depth
Sherpa-Mini *printed | 8
DFA | 8
VZ-Hextrudort-Low | 7
LGX-Lite | 3
Orbiter v2.0 | 6.75
HE Mount | Depth
Sherpa-Mini | 13.5
DFA | 10.2
VZ-Hextrudort-Low | 16
Orbiter v2.0 | 16
Adapter Plate | Depth
Sherpa-Mini | 0
DFA | 0
VZ-Hextrudort-Low | 5.2
Orbiter v2.0 | 5.2
 | PTFE Tube length by Hotend/Extruder (mm)
Hotend | Sherpa-Mini *printed | DFA** | VZ-Hextrudort-Low | LGX-Lite | Orbiter v2.0
Rapido | 45 | 41.7 | 51.7 | 47.7 | 51.5
Dragon ST/HF | 31 | 27.7 | 37.7 | 33.7 | 37.5
Dragon UHF/Mini | 30 | 26.7 | 36.7 | 32.7 | 36.5
XG | 31 | 27.7 | 37.7 | 33.7 | 37.5
NeXt-G | 31 | 27.7 | 37.7 | 33.7 | 37.5
K1 | 31 | 27.7 | 37.7 | 33.7 | 37.5
Revo Voron | 37.4 | 34.0 | 44.1 | 40.0 | 43.8
 | *Sherpa-Mini CNC has been measured as 2mm shorter, but there may be variations by manufacturer
 | **DFA measurements are to the top of the chamfer inside the extruder bottom. You will need to chamfer the top of the PTFE tube or shorten by 1mm
 | ***All these measurements are based off CAD. It is always best to measure and cut to length based on your own setup

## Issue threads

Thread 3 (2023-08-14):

Cpap support?

M3HNGRY, 2023-08-14:
Cpap part cooling fan.

HSGEV, 2023-08-14:
That would be fantastic

DW-Tas, 2023-10-10:
https://github.com/Armchair-Engineering/Xol-Toolhead/tree/main/STL/Experimental/XolPAP

Closed 2023-10-10.

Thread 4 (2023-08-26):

Not enoug hotend cooling for Rapido UHF.

poppatchara, 2023-08-26:
Hi. I used Rapido UHF and old Mantis XOL2's HE mounts with no problem. But when I switched to XOL-Toolhead's new design with updated grills, I started getting more clogs. I decided to clip away some of the grills and the problems were gone.

I think the new grill design has too restricted airflow for the small 2015 fan.

DW-Tas, 2023-08-31:
Hi. Could you please confirm if your setup is using TAP or Xol-Carriage?
There is a future release planned that will remove gills from Rapido mounts and move to an open side similar to Dragon UHF mount: https://github.com/Armchair-Engineering/Xol-Toolhead/blob/main/STL/HE%20Mounts/Xol%20HE%20Mount%20-%20Dragon%20UHF%20-%20Sherpa%20Mini.stl

poppatchara, 2023-08-31:
Hi. It was Tap, vz-hex, Rapido UHF, bridge, with heatset fan.

The fan was gdstime 12000rpm dual ball bearings, 2.45 cfm. Ran on max power.

My Tap is this clone cnc tap.
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

DW-Tas, 2023-08-31:
TAP significantly reduces the space for exhaust airflow compared to Xol-Carriage, as it completely blocks the center-rear exhaust. We recommend the Delta 2510 cooling fan is it is capable of 4.3CFM and significantly outperforms any other tested 2510 fans.

I'm going to close this issue, as there is a release planned that addresses the airflow via gills, but I also recommend you move from TAP to xol-carriage and replace the GDS time fan with the Delta 2510 fan from the BOM to improve hotend cooling capacity.

Closed 2023-08-31.

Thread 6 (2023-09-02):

Sherpa mini with ECAS connector.

erazor666, 2023-09-02:
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

Where can i find that Sherpa Mini part with the ECAS connector as in this picture? I cant seem to find it in the sherpa repo or in the Xol repo. If you want to run the Xol with ERCF this is a pretty vital part.

DW-Tas, 2023-09-02:
Sherpa-mini usermod on Annex Engineering repository: https://github.com/Annex-Engineering/Annex-Engineering_User_Mods/tree/main/Extruders/Sherpa_Mini/Extruder_Mods/alch3my-Housing_Core_with_ECAS_coupler

Closed 2023-09-02.

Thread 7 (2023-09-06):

Update DFA mounting hole pattern to use Rev4 layout

hackerjack42, 2023-09-06:
The DFA mounting hole pattern was updated to a more symmetrical layout in October of 2022.  The current design appears to mesh up with the previous version of the DFA.  Is an update planned?

DW-Tas, 2023-09-07:
Xol-Carriage replaces the bottom part for DFA that is based off rev 4 and can be found here: https://github.com/Armchair-Engineering/Xol-Toolhead/blob/main/STL/Xol-Carriage/Xol%20Carriage%20Adapters/Xol%20Adapter%20DFA.stl

DW-Tas, 2023-09-07:
Xol-Carriage uses a custom bottom part for DFA that is based off rev 4 and can be found here: https://github.com/Armchair-Engineering/Xol-Toolhead/blob/main/STL/Xol-Carriage/Xol%20Carriage%20Adapters/Xol%20Adapter%20DFA.stl

hackerjack42, 2023-09-07:
Perhaps I should have been more specific.  My configuration includes a Rapido and TAP.  I currently have an older version of the toolhead combined with a now deleted experimental adapter plate that managed to allow everything to bolt together.

There is no equivalent solution for this combination of parts.  The adapter plate you linked assumes that it will be paired with the Xol carriage.

https://github.com/Armchair-Engineering/Mantis-Xol/blob/main/STL/Xol%202/TAP/Rapido/Xol%202%20Rapido%20-%20Hotend%20Mount%20-%20DFA%20-%20TAP.stl

https://github.com/Armchair-Engineering/Mantis-Xol/blob/5430e57c48912b01a8f1ac0b656c8ef7206a638e/STL/Experimental/Xol%202%20-%20Adaptor%20-%20DFA%20-%20TAP.stl

DW-Tas, 2023-09-07:
DFA is not supported with TAP on Xol-Toolhead. It put the extruder up too high and was out of balance.
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

Is this the part that let your old setup work? https://github.com/Armchair-Engineering/Mantis-Xol/blob/main/STL/Modded%20Double%20Folded%20Ascender/Mantis_Xol%20-%20DFA%20Bottom.stl

hackerjack42, 2023-09-07:
"N/A" means "Not Applicable".  If what you're saying is accurate, then it should say "Not Supported".

The deleted adapter plate I linked is what made it fit.  The two front holes were large enough for the screws to pass through from above to secure the extruder to the toolhead, and a heatset was inserted into the rear-right hole.  The adapter itself was secured to TAP with two M3 screws from the front.  This let the unmodified extruder mount using three of the four standard locations.  The orientation of the adapter plate meant that the extruder sat about 5mm higher than it normally would.  The plate mounts to TAP with the bed surface facing upwards at the extruder.  The only drawback that I could see is that cable chains would not fit and you therefore had to switch to an umbilical.

Full disclosure; I never did get the completed toolhead assembly installed on my 2.4, so I can't speak to it's balance.  I have a bunch of parts staged for installation, but haven't gotten around to doing so for various reasons.  What I can say is that the assembled toolhead _feels_ quite solid as it sits on my bench.  I agree that this isn't the most scientific bit of evidence.

Closed 2023-09-07.

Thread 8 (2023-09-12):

Missing/wrong printing parts?

valepe, 2023-09-12:
Maybe it's my fault but looking for all parts to be printed there no evidence that optional parts have to be chosen for sherpa extruder.
Under sherpa mini I had to choose:
- STLs/optional_parts/[a]_housing_front_k_x1_rev15.STL instead of STLs/[a]_housing_front_x1_rev15.STL
- STLs/optional_parts/[a]_idler_arm_short_x1_rev15.STL instead of STLs/[a]_idler_arm_long_x1_rev15.STL

I made these choices based on xol 3d model, I suggest to add a note if choosing the sherpa mini extruder

DW-Tas, 2023-09-12:
Have added the following, including links to Annex GitHub for files.

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

patrezp, 2023-10-02:
annex just updated some STLs to rev16
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
this is the new url for idler arm
[https://github.com/Annex-Engineering/Sherpa_Mini-Extruder/blob/master/STLs/optional_parts/%5Ba%5D_idler_arm_short_x1_rev16.STL](https://github.com/Annex-Engineering/Sherpa_Mini-Extruder/blob/master/STLs/optional_parts/%5Ba%5D_idler_arm_short_x1_rev16.STL
)

Closed 2023-09-12.

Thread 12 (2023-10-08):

PCB Klicky Holes Backwards

c0nsole26, 2023-10-08:
Not an issue per se, but caused me to reprint the part mirrored.  More of a heads up or a super gentle nudge perhaps.  I'm still building Xol, but am really excited (ty so much for the work done on it!)

**Issue:**  For the pcb klicky carriage mount STL, the holes appear to be flipped/mirrored.  When the pcb klicky mount is assembled on the carriage, there should be two holes on the left and one on the right if it is intended to work with the standard pcb klicky probe.

Pasting a ref link to the standard probe housing:  https://github.com/tanaes/whopping_Voron_mods/blob/main/pcb_klicky/STLs/probe-heatset.stl

DW-Tas, 2023-10-08:
It already is that way. The shaped part fits into the front piece of the carriage.
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

c0nsole26, 2023-10-08:
DW-Tas resolved on Discord.  I was using the incorrect front carriage (was using the Klicky NG one incorrectly).

Closed 2023-10-08.

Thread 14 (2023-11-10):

Missing front (a) part for the Sherpa

MaikelKelder, 2023-11-10:
Cant seem to find the front part STL for the Sherpa Extruder.
I would expect the STL in the Extruder folder, but not there, maybe I am missing it, but really tried finding it, believe me.
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

DW-Tas, 2023-11-10:
Sherpa-Mini is maintained by Annex Engineering. We have provided links to those parts in our documentation: https://github.com/Armchair-Engineering/Xol-Toolhead/blob/main/docs/printing.md

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

MaikelKelder, 2023-11-10:
Aaaah, Thank you, I looked at the default one, but noticed I needed one with a extra screw on the bottom. Thanks for the quick reply!!

Closed 2023-11-10.

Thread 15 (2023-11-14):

Clockwork extruder support

zhou13, 2023-11-14:
Hi team, does Xol support the Clockwork/Clockwork2 Extruder from Voron 2.4? It looks like it is not on the list of supported extruders.  Is there a plan to add the support for Clockwork?

DW-Tas, 2023-11-14:
Hi. No, it isn't supported, and it won't be supported as the CW/CW2 is too big. You can use the BMG gearset out of CW2 to build a Sherpa-Mini.

Closed 2023-11-14.

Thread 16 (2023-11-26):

Bambulab hotend support

33martin, 2023-11-26:
Hi team, does Xol support the Bambulab Hotend?  It looks like it is not on the list of supported hotends.

thx

BelgarionNL, 2023-12-31:
I would also be very happy if a bambulab hotend support could be added.

DW-Tas, 2024-06-19:
Bambulab mounts available via usermod: https://github.com/Armchair-Heavy-Industries/Armchair-Usermods/tree/main/files/Xol-Toolhead/BambuLab_Xol_HE_Mount

Based off the same CAD building blocks as the release hotend mounts.

Closed 2024-06-19.

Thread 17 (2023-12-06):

Ducts design around M2 bolt holes does not allow enough space for M2 head

pajtaz, 2023-12-06:
In ducts design where M2 bolts go through the ducts to attach the fans, there is only 1.5mm of space between center of M2 bolt hole and two walls of the duct. DIN 912 M2 bolt head is minimum 3.62mm and maximum 3.8mm diameter. Several users have reported M2 bolts not fitting and causing splitting of the duct wall.

See attached photo from latest CAD.
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

When this is sliced with 100% line width, 0.4mm nozzle, one of the walls ends up with only two perimeters. See attached picture from the slicer preview.
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

DW-Tas, 2024-06-19:
No longer an issue with the release on 2024-06-19. These screws are no longer needed with combined ducts/HE mount design.

Closed 2024-06-19.

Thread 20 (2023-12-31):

Dragonfly BMO Support

danilosousadba, 2023-12-31:
Hi,  does Xol support the DragonFly BMO Hotend? It looks like it is not on the list of supported hotends.

DW-Tas, 2024-01-17:
Not officially, but it may fit in the dragon SF mount if you remove the top v6 mount, and file down some of the sharp corners that are extra wide on the heatsink.

Closed 2024-01-17.

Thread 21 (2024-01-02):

Question about NF Crazy hotend mount

tjmitchem, 2024-01-02:
I bought the [Magnum](https://tevoup.com/products/mellow-all-metal-nf-crazy-hotend-v6-copper-nozzle-for-ender-3-cr10-prusa-i3-mk3s-alfawise-bmg-extruder-3d-printer-parts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) version of the NF Crazy hotend.  Can I use the included mount design, or will I need something else?

DW-Tas, 2024-01-17:
Yes, I believe that is all still the same, just with a melt zone extender built into the heat break side.

Sorry I took so long to get back to you with this.

Closed 2024-01-17.

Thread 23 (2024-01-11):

Xol HE Mount - NF-Crazy_fanHS.stl feedback

YesterdaysCoffee, 2024-01-11:
All these mods I've done on my copy.
1) HS holes for hot-end fan could be 4-6mm deeper, otherwise plastic gets back filled into heat set, deeper holes will also allow for 20mm screws to be pulled snug.

2) The posts for the topmost fan mounts (when sitting on the build plate):  This 'wing' snaps easily, due to a smaller layer area at this point.
A small support web has been added, this web needs to be much larger.  On my copy I will widen the web in to the HE fan platform and out a good 10mm.  Perhaps out to flush with the part fan.

3) The bottom most HS post (oriented on the printer) would benefit by adding webbing to close the gap between main gap and horizontal HS socket.

DW-Tas, 2024-01-17:
Hi @YesterdaysCoffee, would you mind adding some screenshots to assist with your descriptions?

YesterdaysCoffee, 2024-01-18:
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

YesterdaysCoffee, 2024-01-18:
I am not suggesting the wire channel be moved or the wire splitter mounts be added.

DW-Tas, 2024-01-19:
1. Hole depth:
These holes are already extended to accept 20mm screws: <br />
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
<br/><br/>
2. Top "wings" breaking:
That is standard geometry on all Xol HE mounts and it doesn't have issues with "snapping easily". If it is breaking there for you, I recommend to print hotter and slower to improve layer adhesion.
<br/><br/>
3. Bottom heatset holes:
This is also standard geometry for Xol parts, but as the NF-crazy is a lower hotend than most, I will look to see if this can be done without increasing the toolhead weight. From a quick look, this may be possible withouth changing print perimiter lenght and may provide some bonus stability. Thanks for the idea :)

Closed 2024-03-08.

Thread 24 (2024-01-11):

Faceplate - Standard - Rear - Low.stl

YesterdaysCoffee, 2024-01-11:
holes for fan screws are .5mm off center

DW-Tas, 2024-01-18:
Could you please add some more details? the rear faceplate has holes for hotend fan screws, and for the blower fan screws/heat sets.
Images would help if you can provide them here as well.
Thanks.

YesterdaysCoffee, 2024-01-18:
When the rear face plate is mounted with the blower fan screws, all HE fan screws do not line up.  And visa versa, when the rear face plate is mounted with the HE fan screws, all part blower fan screws do not line up.
My workaround was to enlarge the HE fan screw holes.

DW-Tas, 2024-01-19:
I can't reproduce the issue. Everything is lined up in the CAD.
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

DW-Tas, 2024-03-08:
No reply, closing

Closed 2024-03-08.

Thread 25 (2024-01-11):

Xol Carriage - Rear - MGN12H - 6MM.stl

YesterdaysCoffee, 2024-01-11:
when oriented on the printer:
top two holes are unnecessarily deep and makes removal of screws difficult, especially when mounted on the printer with screws facing backward.  Making the counter bore shallow, instead of deep, allows fingers to grasp the screw when loose.

Also, does the hole really need to be hexagonal instead of round?

DW-Tas, 2024-01-17:
Holes unnecessarily deep:
* The holes are that depth for the following reason
* * Standardising around M3x8 SHCS where possible to minimize BOM
* * Allowing a heatset in a small plastic insert to be placed in the hole for StealthBurner compatibility (screws inserted from front)

Hexagonal shape:
* Prevents spinning of inserted parts for StealthBurner or other mods

Removing screws:
* The intention is that screws in that location should not be removed, but stay there ready to be screwed back into the toolhead when it is re-attached.
* If you remove the toolhead, you can push the screws out from the front with the end of the hex driver.

Closed 2024-01-17.

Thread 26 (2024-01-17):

Update probe mounts to include different beacon version mounts

1scottlyl, 2024-01-17:
The files listed in the printing guide (https://github.com/Armchair-Engineering/Xol-Toolhead/blob/main/docs/printing.md#probe-modules) don't list the beacon rev H files, only the Rev D.

I missed the other files for Rev H in the repo due to getting files from the print guide, and figured it could be an avoidable error in the future.

DW-Tas, 2024-01-18:
Fixed:
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

Closed 2024-01-18.

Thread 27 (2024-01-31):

Bom incorrect

Zeanon, 2024-01-31:
The bom states 6 m2 inserts without the bones and 8 with the bones while in reality you need 8 without the bones and 10 with the bones

DW-Tas, 2024-01-31:
Fixed with BOM update.

Closed 2024-01-31.

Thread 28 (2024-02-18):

Carriage for Switchwire

Gaetan36, 2024-02-18:
Good morning,
Is there a carriage for voron switchwire?
They work in XZ so the belts are not in the same place.
Thank you.

DW-Tas, 2024-02-18:
Xol-toolhead will attach to the standard voron carriage. Just use the Tap compatible extruder mount and instructions for Tap installation.

Closed 2024-02-18.

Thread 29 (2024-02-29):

Fairly Certain Delta Electronic's fan specs are erroneous for 	 ASB02505SHA-AY6B

DavidCC00, 2024-02-29:
Compare these two delta fans:

https://www.digikey.com/en/products/detail/delta-electronics/ASB02505SHA-AY6B/7491489  (5v from BOM)

https://www.digikey.com/en/products/detail/delta-electronics/AFB02512HHA-CF00/15970968 (Delta 12v otherwise identical)

There's only so many things you can do to improve a fan while keeping it's form factor the same.

1.  Power (Watts or RPM)
2.  Change Fan blades
3.  Reduce friction (ie. maglev > ball bearing > sleeve/hydraulic.   Brushless > brushed motor)

The 12v fan beats the 5v one in both Watts (0.600 vs 0.960) and being ball bearing instead of sleeveless.   Delta's website doesn't specify fan blades, but they both appear to be the same large, flat 5 blade configurations (which is good for static pressure, airflow fans tend to have few skinny blades like a ceiling fan).

In addition, the specs on the 5v fan rival that of much larger fans.

I've emailed both digikey and Delta Electronics to find out, but unless something very odd is going on, I'm going to say it's an error.  I'll update here when I hear back.

lraithel15133, 2024-03-28:
@DavidCC00 any update on this? I am very curious.

DavidCC00, 2024-04-15:
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

I'm still really doubtful.  I've watched the fan showdown for years, have experience with brushless motors and watched lot of technical data on it (RCExplained does very technical dives),  etc.   The hydrostatic pressure rating on that, for an axial fan, is absolutely nuts.  Especially at ~30db.  Like, if it was 65db and spinning at 10krpm, I'd believe it.  For its size, that also seems like really good CFM.   Also, generally 12v fans are better than 5v fans just because they can generally produce more watts energy.  (Although, for whatever reason, maybe because they aren't as popular, 24v fans don't see much boost).

However, it must be a pretty good fan regardless of accuracy of spec sheets, since I'd assume people would be reporting heatcreep issues, otherwise.

woodencliff, 2024-07-08:
If you comparing them side by side , the size of their fan hub is apparently different. ASB02505SHA-AY6B has the biggest disc area of its class, so it has best airflow!
As for power consumption, I think there might be some volt conversion process in the higher volt model, which costs extra power.

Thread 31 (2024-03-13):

Xol Carriage Assembly two typos

uosdwishpoom, 2024-03-13:
"pit" should be "bit"
"lenght" should be "length"

DW-Tas, 2024-03-13:
Fixed. Thank you.

Closed 2024-03-13.

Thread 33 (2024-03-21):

LED Duct Interference Fit Issues

uosdwishpoom, 2024-03-21:
Both bottom PCF to LED Duct screws are an interference fit which is causing misalignment and ducts to split at the screw location.  Honeybadger fans from Fabreeko don’t fit the opening in the duct.  The fan and duct are .5mm from fitting along the long axis of the opening in the duct.

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

uosdwishpoom, 2024-03-21:
Fusion Filaments ABS 1.5 Uranium Yellow.  Shrinkage compensation 99.2.

uosdwishpoom, 2024-04-10:
Here is the solution I used and it worked great.
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

rcg94, 2024-04-22:
> Here is the solution I used and it worked great. ![image](https://private-user-images.githubusercontent.com/133539169/321393559-2070b8da-b40f-4991-a497-cadcf2be05db.png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)

Do you mind posting the file you made? Hoping to use it with my new honeybadger fans coming tomorrow

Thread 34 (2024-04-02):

Xol LED Ducts - Tri-Vane Asym Right - Trident.stl | missing cutout prevents LED from beeing installed

shnizzl, 2024-04-02:
Hello, it seems there is a missing cutout/extrusion in the file _Xol LED Ducts - Tri-Vane Asym Right - Trident.stl_, which makes it impossible to install Neopixel LED with soldered on wires. The LED without wires does fit in die printed part, but anything that is soldered on would be sheared off while pushing the LED into its slot:
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
This only affects _Xol LED Ducts - Tri-Vane Asym Right - **Trident**.stl_, both _Xol LED Ducts - Tri-Vane Asym **Left**.stl_ and _Xol LED Ducts - Tri-Vane Asym **Right**.stl_ are fine.

DW-Tas, 2024-04-03:
Thanks @shnizzl .  Updated STLS and STEP files have been uploaded.

Closed 2024-04-03.

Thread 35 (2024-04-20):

NeXtG UHF support?

DavidCC00, 2024-04-20:
The NeXtG UHF is apparently *almost* a rapido's dimensions, but without the taper up top.  I have one on order, and was hoping to build my printhead as a XOL.   Unfortunately, my understanding of CAD has been growing slowly, so I'm bringing this up.  (I can probably use tinkercad for personal use, but... tinkercad results in wonky files I'd hesitate to share with anyone).

Here's where I got my info about the dimensions:

https://www.printables.com/model/821299-drop-effectphaetus-next-g-uhf-stealth-burner-print

DW-Tas, 2024-04-20:
Please read [printing.md](/Armchair-Heavy-Industries/Xol-Toolhead/blob/main/docs/printing.md) from the docs. Next G part requirements are there.

There is equivalent information in the pre-release version docs if you’re using that version.

DavidCC00, 2024-05-07:
Ah, good info.  I missed that, thank you.

Closed 2024-05-07.

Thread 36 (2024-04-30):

Gap too large between Revo heat sink and cooling fan shroud causing heater problems

Urminme, 2024-04-30:
When using the standard Revo Heater core this is not an issue, but when using the Revo High temp Hotside which is just a standard heater block that fits a Revo nozzle I've noticed too much air from the Hotend cooling fan comes down through the large gap between fan shroud and the Revo Heatsink and blows over the actual heater block that it significantly impacts the heaters performance, ive done a few test where I've added some metal to this area to try and block the air from blowing down over the heater and its made a big difference, with it as is the heater is almost always @100% power trying to compensate and I've even had several prints fail as the heater cant keep up due to the excess cooling from the fan. Could you consider adding a version for the Revo(High Temp Hotside) that brings the hotend fan shroud closed to the heatsink to prevent excess air from flowing down over the top of the heater? Normally the heatsink does not get very warm at all and I don't think there is any issue of the heat sink melting the plastic especially with ASA or ABS, Toolhead's such as the stealth burner have the shroud basically touching the heatsink.

I added a picture but its not the Revo hotend unfortunately however i circled the area of concern, I don't know if anyone else is even using this combo but I print a lot of PC, Nylon and ABS so I need the higher temps available with the Revo high temp hotside
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

DW-Tas, 2024-05-08:
I have made an update in the pre-release branch for revo-voron hotend mounts. Have a look at this one for an example. Let me know how it goes please. <https://github.com/Armchair-Heavy-Industries/Xol-Toolhead/blob/pre-release/STL/HE%20Mounts/Xol_HE_Mount-Revo-Voron_Fan.stl>

Urminme, 2024-05-08:
Thats much better, I love this toolhead and its been amazing in every other aspect. I appreciate your hard work. I will print this out today and check everything out, I'll let you know how it works, I dont know how many folks are using the Revo high temp hotside, but its very good.

Closed 2024-05-20.

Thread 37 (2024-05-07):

BTT Eddy (Beacon Clone) Support in planing?

toscdesign, 2024-05-07:
Hi,
there ist a new Probe available.
The Bigtreetech Eddy.

This is a Beacon Clone with integrated Raspberry Pico and USB Connection:
https://github.com/bigtreetech/Eddy

It would bei nice to use it with the XOL Toolhead.
I have ordered one and would make myself available as a beta tester if needed.

DW-Tas, 2024-05-07:
So Xol isn't likely to support Eddie. There is a collision between Eddie and the X rail carriage.
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

toscdesign, 2024-05-07:
Ah ok, thanks for the picture!

Is this the normal XOL or the longer Version for a Rapido UHF?
The long Version could have enough space, but I'm not sure.

Do we need the case from the Eddy?
As far as I know, it ist possible to use the pcb of the Eddy without it. The pcb itself hast mountingholes for screws.

This could be a way to use the Eddy with XOL

DW-Tas, 2024-05-07:
The PCB holes are in the same spot, and there is a JST connector at the top (in the gap shown in the picture). It would probably work with the UHF versions, but I am not going to make something that won't work with all versions.
The CAD for the existing probe modules is available if someone wants to make a UHF only usermod.

Closed 2024-05-07.

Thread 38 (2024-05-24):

Voron tap mount missing from the pre-release STL

YoungHillionaire, 2024-05-24:

DW-Tas, 2024-05-25:
@YoungHillionaire could you please add some more details? The Tap extruder mounts are in the extruder mounts folder.

DW-Tas, 2024-06-08:
Closing as no response. Please re-open if there is more detail to provide.

Closed 2024-06-08.

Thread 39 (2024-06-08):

experimental cpap difference between UHF duct and non UHF

Dario-Ciceri, 2024-06-08:
Hi, I checked the two models but I don't see any difference, is UHF a placeholder for the uhf version or does it refer to something else?
thanks

DW-Tas, 2024-06-08:
Hi. did you put them side by side in a slicer?
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

Dario-Ciceri, 2024-06-08:
> Hi. did you put them side by side in a slicer? ![image](https://private-user-images.githubusercontent.com/116466447/337875792-e0af2228-b608-4c21-811e-67726975a990.png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)

damn I didn't as I was using CAD and didn't notice... sorry...

Closed 2024-06-08.

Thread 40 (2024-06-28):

Add a filament cutting feature

Kaympe20, 2024-06-28:
Is there a way to add compatibility for a filament cutter similar to that of [Filametrix](https://github.com/sorted01/Filametrix)? I would like to use the Xol-Toolhead, but I use the Enraged Rabbit Carrot Feeder.

DW-Tas, 2024-06-28:
Have a look at Xol-metrix mod by SouthAsh1. They even have some based on the new release already under the BETA STLs

https://github.com/SouthAsh1/Xol-metrix

https://github.com/SouthAsh1/Xol-metrix/tree/main/STL/BETA

Closed 2024-06-28.

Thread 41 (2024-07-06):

latest release seems dont support epdm belt

woodencliff, 2024-07-06:
While updating to latest release, I'm struggling to get epdm belts to fit in the new belt clips, only to find epdm belt is too thick, hope there will be a clip mod.

DW-Tas, 2024-07-13:
Print the clips with a couple of percent lower extrusion multiplier to make them a looser fit.
Make sure to print lots of perimeters so they are basically solid. Also print the slow and hot for best strength.

aju3169, 2024-08-26:
I’m printing the belt clips on a BambuLab and the extrusion is set.  I can’t change the extrusion multiplier as far as I know.     It’s impossible to put the belt clips on for my edpm belts.

DW-Tas, 2024-08-26:
> I’m printing the belt clips on a BambuLab and the extrusion is set. I can’t change the extrusion multiplier as far as I know. It’s impossible to put the belt clips on for my edpm belts.

If Bambu slicer doesn't support EM (It should be under filament settings). You could use Orca Slicer.

Alternatively, fold up some sand paper and open the belt path a little that way.

aju3169, 2024-08-26:
Thank you - I sorted it out my using a very small file to open up the belt path.  Perfect now.

Closed 2024-11-19.

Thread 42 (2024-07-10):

Belt lock for a Switchwire

rollduck, 2024-07-10:
Hi,

Is there any small chance to adapt or make a new belt lock for Voron Switchwire something like this? https://www.printables.com/pl/model/773280-xol-belt-support-for-voron-switchwire
This one works very well, but maybe an official solution will be better? :) Please don't forget about this beautiful 3d printer :)

Thanks in advance :)

skud52, 2024-07-14:
I've been working on a solution

https://www.printables.com/model/943175-xol-switchwire-backplate

YoungHillionaire, 2024-07-31:
> I've been working on a solution
>
> https://www.printables.com/model/943175-xol-switchwire-backplate

Thanks
Does this take the belt clips of the official SW or the XOL?

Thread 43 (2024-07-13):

LGX Lite when?

GTreaper, 2024-07-13:
Hows the eta looking on can mount for the LGX Lite?

Thanks for the great work

MoppelMat, 2025-01-08:
I have the same question. I currently run SB with Tap and a LGX Lite want wanted to switch to this Toolhead. But as it seems there is no way to mount the EBB then. Since the LGX lite and the Tap is supported, I am a bit lost how to mount the Can board then. Or Can I just hotch potch my LDO NightHawk-SB on there "somehow"?

MoppelMat, 2025-01-08:
that looks promising!
thank you for your VERY swift reply.

sadly I have not done anything yet as I am still collecting options. But this seems like I can get started and see where I end now.
Thank you again.

Closed 2025-06-04.

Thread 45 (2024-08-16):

EBB SB2209 CAN support?

tonieMajke, 2024-08-16:
Are there plans to support SB2209 can?

DW-Tas, 2024-08-26:
No, The SB2209 is designed specifically for StealthBurner only.
There is a usermod for an older board that the SB2209 form factor is based on that may work: https://github.com/Armchair-Heavy-Industries/Armchair-Usermods/tree/main/files/Xol-Toolhead/Afterburner_Toolhead_PCB_Mount

Closed 2024-08-26.

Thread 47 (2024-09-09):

Feedback/integration request for Mellow/Annex Engineering Sherpa Micro extruder

nexus665, 2024-09-09:
Hi,

I recently changed my Voron toolhead from SB to Xol and am pretty happy with it in comparison. I got the Sherpa Micro extruder, as the article description stated it had the same mounting pattern as the Mini - should have double-checked :) Of course, it doesn't. It also does not feature the extended front plate that has a fastener below the interface plane with the mount.

[Github Link to the Extruder](https://github.com/Annex-Engineering/Sherpa_Micro-Extruder)
[CNC Version I got (german shop)](https://meltbro.de/sherpa-libra-mini-orbiter-extruder-ultra-leicht-verbesserte-version-voron-2-4-v0-ender-3-cr10.html)

CNC/printed versions are identical, but the mounting pattern is a bit narrower than the Mini. Also, the pancake stepper interferes with the mount of the Mini, so there was no simple fix and I could not just move the mounting holes.

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

So I took the mini mount and modified it to fit on a CNC Tap V2 (fits V1 too), along with a mount plate for an EBB36 board that is way more stable than others I've found - because it uses 3 mounting points instead of 2. The mounting pattern for the stepper does not interfere with the EBB board at all, unlike all versions I found online so far - which use the stepper mounting bolts exclusively. Mine uses the TAP mounting holes instead. Nice extra benefit of this: shorting out your toolhead board on a fastener becomes almost impossible. As for how I know that can happen on other EBB mount plates...*smh*...well, at least I had a nice dummy PCB to test with ^^

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

This is a not perfectly cleaned up version, I'd like your feedback on it before I put in more work to clean up the last few small artifacts from plugging a top section onto the existing Sherpa Mini mount. Oh, and shave off the extra bit on the left that's not supporting anything on the Micro.

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

I used two M3 heatserts on top to fix the extruder to the mount - the hole pattern interferes with the Tap mounting screws and makes a through-plate mount option pretty difficult. Do you think that's acceptable?

It is to me, because I designed the EBB mount to also brace the extruder. It is VERY stiff as is, my resonant freqs moved up a couple of Hz vs. my old mount (from the project you link to in the docs for 3rd party EBB mounts). Also, it has been working quite nicely in my Voron for a week now, so I'm happy with that.

STL:
[CNC-Sherpa-Micro-Extruder-Mount.zip](https://github.com/user-attachments/files/16924400/CNC-Sherpa-Micro-Extruder-Mount.zip)

(obviously, CAD is available if interested)

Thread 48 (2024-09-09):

Request: NF Crazy/Slice Mosquito hotend

notheotherben, 2024-09-09:
Hi there folks,

I noticed that you've got an NF Crazy Volcano hotend option, but didn't have a "standard length" variant for the standard NF Crazy/Mosquito/Mosquito Magnum. After hacking together a franken STL which combined the lower ducts from the Dragon SF and the upper mount from the NF Crazy, I can confirm that this works perfectly. Rather than submitting my (not very happy) STL, can I ask you to include this variant in a future release?

Thank you for all the hard work on Xol, it's been a treat to use.

DW-Tas, 2024-09-09:
Hi notheotherben,

We used to support NF Crazy with a standard block, but support for that was removed. The block is super wide and interferes with both airflow and lighting from LEDs.

The recommended approach is to use NF Crazy with an extender if you don't want to use the volcano block. I used the extender version quite a lot while developing the current release, and just like dragon with an extender, it has excellent airflow and lighting.

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

notheotherben, 2024-09-09:
Thank you, and apologies for missing that in the docs

Closed 2024-09-09.

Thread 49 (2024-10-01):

Dragon UHF hotend mounts have only 1 our of 4 holes recessed

fff7d1bc, 2024-10-01:
Looking at the other hotend mounts, only Dragon UHF one seems to have 1 out of 4 screw holes recessed, seems like it is not intentional

fff7d1bc, 2024-10-01:
After brief exchange on discord I understood that this is expected and one bolt sits slightly lower.

Closed 2024-10-01.

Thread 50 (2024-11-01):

Bambu HE mount interferes with TAP screws.

actualbigbobin, 2024-11-01:
top 2 screw heads interfere with the HE mount, it was also like that before the major update.

DW-Tas, 2024-11-01:
Can you please upload some pictures of what you mean? I don't understand the issue. Thanks.

actualbigbobin, 2024-11-01:
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

DW-Tas, 2024-11-01:
Thanks, that makes a lot more sense now. I've added this to the list.

actualbigbobin, 2024-11-01:
[Xol_HE_Mount-BambuLab_Fan.zip](https://github.com/user-attachments/files/17596184/Xol_HE_Mount-BambuLab_Fan.zip)
Here is my fix for it, I also extended the extruder mount hex nut hole through the other side because the nut got stuck once and it is impossible to remove it as is.

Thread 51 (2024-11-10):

Rapido ACE UHF

Sotiocsi, 2024-11-10:
Hi!

Could I have a "Xol_HE_mount_fan" for Rapido ACE UHF step format?

Rapido ACE UHF is exactly 3 mm shorter than rapido UHF.

THX.

DW-Tas, 2024-11-10:
Doesn't the Rapido ACE come with a 3mm spacer for that reason?

Sotiocsi, 2024-11-10:
but, yes. I wanted to leave it out to make it as short as possible.

Sotiocsi, 2024-11-10:
i see "Xol_HE_Mount-Dragon-Ace_Extender_Fan" is good for rapido ace UHF.

Closed 2024-11-19.

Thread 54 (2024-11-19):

Klickly for Rapdio 2 HF

pgthang1991, 2024-11-19:
Hello team,
I have a Rapido v2 HF and I want to use it with the Klicky PCB. I can't find the STL file in the Probe Modules folder. Can you give me the stl file?

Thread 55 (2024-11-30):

Request: Third Cooling fan - Voron TAP

JesNoFear, 2024-11-30:
Concept is to have a third cooling fan to cool the backside of the toolhead. Sadly I lack Fusion / CAD skills to make this, which is why i am asking :-)

I found this (linked) third cooling fan for SB + Voron TAP (Chaoticlabs CNC Voron TAP), which works well. but I would like it to be more uniform with the XOL setup.
https://www.teamfdm.com/files/file/738-stealth-burner-3rd-parts-cooling-fan-mount/

Concept image (I frenkenstined this together)
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

I am thinking to make this work / make it better for the XOL would be to reverse the fan insert direction, instead of inserting the opening, inserting the closed side from the top so the duct can be part of the print / permanently attached unlike in my example.

with the 3010 fan its small enough to not extend past the clearance of the 2020 extrusion, making it a no adjustment add-on.

GDSTime makes a 24v 3010 blower that seems to be working well so far.
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

I have tinkered around with trying to fit a 4010 blower back there, but it doesn't offer enough clearance, even at an angle to compensate for the extra length, TAP loses its full motion causing the bracket to snap.

Here is an example of the third fan "as is" without the addition of a duct.
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

DW-Tas, 2024-11-30:
I appreciate you have taken the time to make this request, but it's not something that will be implemented into Xol. This is really a mod for CNC Tap that would not work with Xol-Carriage at all.

I also expect that a duct like your example with an 'S' bend in the airflow would be less effective than the simple deflector that is already in place.

I would, however, highly recommend that you use this as a reason to learn some CAD skills of your own. It's much easier to learn when you have a good source of motivation.

Closed 2024-11-30.

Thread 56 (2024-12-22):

Request: "Official" support for Bambulab hotend

tomdelahaba, 2024-12-22:
I know the bambulab hotend is "somehow" supported and its done via user mods... But it is always very hard to find out the link (its not mentioned in the PRINTING folder nor the PARTS... It is only under "Full Readme"...

As well, I believe that a lot of us really felt in love with the Bambu hotend as its ultra cheap and quite powerful hotend. And I believe all of us felt in love with XOL. Can you guys start already "officialy" support the Bambu hotend? It would make our lives much easier (not yours though 🤣 )

Jakrabo, 2024-12-29:
Same for me. Thanks for your awesome work on the xol tool head!

danilo-ml, 2025-05-01:
+1

mhubacz, 2025-05-06:
+1

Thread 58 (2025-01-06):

provide 3mf files alongside STL

andrewmeyer, 2025-01-06:
I am having trouble with the baked-in supports on the HE mount.  ideally I would be able to switch them off and have my slicer generate supports that hopefully will not snap off the bed half way through the print.

Some of the extruder mounts come in this format already

Closed 2025-01-13.

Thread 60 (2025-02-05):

BFB0412HHA-A is obsolete and no longer manufactured

kozross, 2025-02-05:
The title of the issue is what the purchase link for this fan says. Maybe it might be worth suggesting a different 12V fan?

Also, why are no 24V fans for either the hotend or part cooling suggested? Most people run 24V systems nowadays.

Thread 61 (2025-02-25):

belt clips for cartesian style printers like the ender 5

maxxx500, 2025-02-25:
I am creating a xol toolhead for my klipper converted ender 5 and can't find any available solutions for belt clips as unlike the ender 3 the belt is in the middle of where the clips are for corexy systems? Is there a way for someone to design a clip for this and share a link. Thank you.

maxxx500, 2025-05-16:
+1

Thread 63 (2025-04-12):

EBB 42 support

Bromles, 2025-04-12:
Are there plans to support EBB42?

EBB36 is fine, but it's limited to 24v 6a, and I'm not sure if I can fit everything in it's power limits. And EBB42 is 24v 9a, which is nicer, but the board itself is bigger

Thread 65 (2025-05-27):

Belt clamp for 9mm monoliyh gantry

enddDD, 2025-05-27:
Hi, is there another belt clamp thst i can use with monolith gantry, since the belt sides are reversed on monolith gantry. Thanks!

DW-Tas, 2025-05-27:
There's a whole carriage for Monolith. https://github.com/Armchair-Heavy-Industries/Armchair-Usermods/tree/main/files/Xol-Toolhead/Monolith_Xol-Carriage

enddDD, 2025-05-27:
> There's a whole carriage for Monolith. https://github.com/Armchair-Heavy-Industries/Armchair-Usermods/tree/main/files/Xol-Toolhead/Monolith_Xol-Carriage
Oh, thank you, dont know how but i missed it. Thanks a lot!

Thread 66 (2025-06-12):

Belt mount failed on the bottom side

nonsintetic, 2025-06-12:
I had a first failure and thought it might be useful info for you guys. While ironing the top surface of a part the belt pin holder snapped on the bottom side and the belt flew off stopping the print. See included picture for reference. I didn't see anything on the part that would indicate it got stuck on something, but who knows really.. My guess is it must have hit something at one point causing a crack and it just got weaker and weaker as I kept printing. Just going to superglue it back and print a new one.

The parts were printed in Polymaker ABS 100% infill and the toolhead has been running for at least 150 hours. The version used was whatever was latest on 11th of February 2025. Heated chamber was at 50C at the time, hotend was at 250C, these are the typical temperatures I print at.

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

Overall very happy with the toolhead, except those 2 screws inside the hotend area that are very fiddly to get tight.

DW-Tas, 2025-06-26:
Thanks for reporting. 100% infill is not recommended as parts can become more brittle. This is still an unexpected failure mode unless you have over-spec belt tension or a head crash. Do you have any more information?

DW-Tas, 2025-07-12:
Closing this issue, but thanks for reporting it.

Closed 2025-07-12.

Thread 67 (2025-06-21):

Add Config for EBB36

kobold81, 2025-06-21:
Hello,

after assembling the XOL I ran into a little problem, I could not find a ready to use config-add-on for including the ebb36 into my printer.cfg.

So, if anyone wonders how to configure the sherpa mini with the ebb36 and the XOL with dual part cooling fans:

1. Sherpa Mini Config: https://github.com/Annex-Engineering/ANNEX-Printer-Firmware/blob/main/Klipper_and_Klipper_Derivatives/Sherpa_Mini/Klipper_Config_Block.txt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
2. ebb36 1.2 config: https://github.com/bigtreetech/EBB/blob/master/EBB%20CAN%20V1.1%20and%20V1.2%20(STM32G0B1)/sample-bigtreetech-ebb-canbus-v1.2.cfg
3. Klipper config for using two part cooling fans:
[multi_pin my_part_cooling_fans]
pins: EBBCan:PA0, EBBCan:PA1
[fan]
pin: multi_pin:my_part_cooling_fans
max_power: 1

kobold81, 2025-06-28:
You are absolutely right, with my Sunon MF25100V11000UG9 the yellow line is tacho and not pwm, I confused that with a different fan. nevertheless putting the supplied connector to led gives a very good physical connection out of the box with 5V and GND. Always on is good for me for security.

Closed 2025-06-29.

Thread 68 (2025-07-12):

Phaetus NeXtG hotend doesn't fit in Hotend mount Xol_HE_Mount-XG_Fan

JasonMBarnard, 2025-07-12:
I have the Phaetus NeXtG hotend and from the center of mounting holes to the outer edge of the hotend is about 6mm.  However the Xol_HE_Mount-XG_Fan.stl file only has about 3mm clearance from the front mounting holes to the front inner wall where the 2510 fan blows through to cool the hot end.  So the Hotend cannot be mounted because it is too close to the front wall.  The front wall needs recessed at least 3 mm.

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

JasonMBarnard, 2025-07-12:
Sorry, I just review it again.  I have the wrong hotend mount.

Closed 2025-07-12.

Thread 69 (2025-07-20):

Phaetus DropEffect NeXtG mounting holes

JasonMBarnard, 2025-07-20:
When installing a Phaetus DropEffect NeXtG hotend into the Xol_HE_Mount-DragonUHF_Mini_Fan.stl mount, the mounting holes really need to be rotated about 30% (give or take) counter-clockwise when looking down from the top.  The heater and thermistor wires come out right at a bracket and cannot make the turn needed and it pinches the wires.  I had to cut the wires free from the strain relief and it is still too tight.  Additionally, rotating the hotend 90 degrees to hit the next mounting holes just causes the wires to hit the mounts on the other side.

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

JasonMBarnard, 2025-07-21:
I found rotating it 180 degrees and having the wires come out the front works.

Closed 2025-07-21.

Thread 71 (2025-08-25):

Cooling Phateus Dragon HF too well

CMOSBATTERY1, 2025-08-25:
I am using the Xol_HE_Mount-DragonSF-HF_Fan mount and when installed and the part cooling fans are turned on the heater cant maintain temp because the heater block is being cold down too well. Strange issue to have and nice to know the fans are doing their job well but not sure hot so solve as I don't believe a insulation sock will make much of a difference.

DW-Tas, 2025-08-27:
The issue with heating the hotend has been reported before and always turned to be one or multiple of:
1. not using a sock on the heat block (must have)
2. Haven't PID tuned since changing to new setup
3. Under powered or faulty heater cartridge

Closed 2025-08-28.

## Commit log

2023-06-22 Initial upload
    [Adapter Orbiter2 - Xol Carriage.stl, Adapter Sherpa Mini - Xol Carriage.stl, Adapter VZ-Hexdrudort-Low - Xol Carriage.stl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]
2023-06-22 Added HE Mounts and updated printing instructions
    [Adapter Orbiter2 - Xol Carriage.stl, Adapter Sherpa Mini - Xol Carriage.stl, Adapter VZ-Hexdrudort-Low - Xol Carriage.stl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]
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2023-06-23 Lots of STLs and doc updates
    [Adapter Orbiter2 - Xol Carriage.stl, Adapter Sherpa Mini - Xol Carriage.stl, Adapter VZ-Hexdrudort-Low - Xol Carriage.stl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]
2023-06-23 Adapter plates: STL and doco
    [TAP Adapter Orbiter2.stl, TAP Adapter Sherpa Mini.stl, TAP Adapter VZ-Hexdrudort-Low.stl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]
2023-06-24 Faceplate fixes
    [Faceplate - LED - Front [southern hemisphere edition].stl, Faceplate - LED - Front.stl, Faceplate - standard - front.stl]
2023-06-24 Fix hextrudort name
    [TAP Adapter VZ-Hextrudort-Low.stl, Xol Adapter VZ-Hextrudort-Low.stl]
2023-06-25 Updated duct STLs and keeping doco changes up to date.
    [Xol Ducts - Tri-Vane Asym Left.stl, Xol Ducts - Tri-Vane Asym Right - Trident.stl, Xol Ducts - Tri-Vane Asym Right.stl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]
2023-06-28 mgn9 updates for carriage assembly
    [Xol Carriage - Front - MGN9H - 6MM [KlickyNG].stl, Xol Carriage - Front - MGN9H - 6MM.stl, Xol Carriage - Front - MGN9H - 9mm [KlickyNG].stl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]
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2023-06-30 Probe Module STLs and links
    [Beacon_Module.stl, Beacon_Module_UHF.stl, Euclid_Module.stl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]
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2023-07-04 bugfix: mgn9 counterbore bridging
    [Xol Carriage - Rear - MGN9H - 6MM.stl, Xol Carriage - Rear - MGN9H - 9MM.stl]
2023-07-04 bugfix: MGN9 carriage mount counterbore + some CAD
    [Xol Carriage - Front - MGN9H - 6MM [KlickyNG].stl, Xol Carriage - Front - MGN9H - 6MM.stl, Xol Carriage - Front - MGN9H - 9mm [KlickyNG].stl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]
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2023-07-05 doco fix and StealthBurner compatible carriage front
    [Xol_Carriage_Front [StealthBurner].stl]
2023-07-11 Added NeXt-G HE Mount STLs
    [Xol HE Mount - NeXt-G - DFA - fan HS.stl]
2023-07-13 Update printing.md
    fix rapido no HS STL link text
2023-07-15 update carriage file names and printing.md
    [Xol Carriage - Belt Clip - 6MM.stl, Xol Carriage - Front - MGN12H - 6MM [KlickyNG].stl, Xol Carriage - Front - MGN12H - 6MM.stl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]
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2023-07-19 update Klicky_PCB_Module_UHF.stl - fix short switch clearance
    [Klicky_PCB_Module_UHF.stl]
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2023-07-20 standard faceplates now work with LED ducts (credit: itznicholas72)
    [Faceplate - LED - Rear - XG.stl, Faceplate - LED - Rear.stl, Faceplate - standard - rear.stl]
2023-07-22 Replaced Dragon UHF STLs. Fix hole size for Revo.
2023-07-23 new dragon UHF. printability fix rapido based stls
    [EBB36 Mount - VZ-Hextrudort-Low [strain relief].stl, EBB36 Mount - VZ-Hextrudort-Low.stl, Xol HE Mount - Revo - DFA.stl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]
2023-07-24 Dragon UHF HE Mount minor fix (fuse)
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2023-07-29 Added PTFE tube measurements
    [PTFE-Measurements.xlsx]
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2023-08-18 belt slip test fix
    [Xol Carriage - Belt Clip - 6MM - E.stl, Xol Carriage - Belt Clip - 6MM - S.stl, Xol Carriage - Belt Clip - 9MM - E.stl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]
2023-08-20 added M2 savers STL
    [[a]M2x10 Saver_2x.stl]
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2023-08-30 Update BOM.md
    Changes:
    - Changed BFB0412HHA-A117 to BFB0412HHA-A. The -A117 variant has ultra short leads (~65mm) and a connector, the regular -A variant has 150mm unterminated leads
    - Changed links to Digikey to the US site to show more "familiar" US$ prices
    - Added BFB0405HHA-A (5V) as alternative to the 12V variant, it has the same specs but can be used with CAN toolheads
    - Added remark about using a step down converter like K78L12-500R3 to step down from 24V to 12V
2023-08-31 beta carriage varient with wider cable run
    [Xol Carriage - Rear - MGN12H - 6MM_a.stl]
2023-09-12 Update printing.md: Issue #8
2023-09-13 Delete STL/Ducts/Xol Ducts UHF - Tri-Vane Asym Right - Trident.stl
    no worky
    [Xol Ducts UHF - Tri-Vane Asym Right - Trident.stl]
2023-09-13 Fixed orientation and updated UHF ducts for Trident
    [Xol Ducts UHF - Tri-Vane Asym Left.stl, Xol Ducts UHF - Tri-Vane Asym Right - Trident.stl, Xol Ducts UHF - Tri-Vane Asym Right.stl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]
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2023-09-15 file name fix test 1
    [Faceplate - Standard - Rear - XG.stl, Faceplate - standard - front.stl, Faceplate - standard - rear.stl]
2023-09-15 filename fix test 2
    [Faceplate - Standard - Front.stl, Faceplate - Standard - Rear - XG.stl, Faceplate - Standard - Rear.stl]
2023-09-20 bugfix - LED faceplate screw hole size
    [Faceplate - BARF LED - Front.stl, Faceplate - LED - Front.stl]
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2023-09-20 update Xol-Toolhead_Assembly-Guide.step (LED faceplate hole bugfix)
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2023-09-21 update UHF duct STLs
    [Xol Ducts UHF - Tri-Vane Asym Left.stl, Xol Ducts UHF - Tri-Vane Asym Right - Trident.stl, Xol Ducts UHF - Tri-Vane Asym Right.stl]
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2023-09-25 fix thin wall on LED faceplate rear parts
    [Faceplate - BARF LED - Rear.stl, Faceplate - LED - Rear.stl]
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2023-09-26 update Klicky_PCB_Module_UHF.stl to fit klicky-00
    [Klicky_PCB_Module_UHF.stl]
2023-10-01 upload correct LED UHF right duct
    [Xol LED Ducts UHF - Tri-Vane Asym Right.stl]
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2023-10-12 Probe module fixes
    [Euclid_Module_90.stl, Euclid_Module_90_UHF.stl, Klicky_Module_UHF.stl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]
2023-10-19 Update printing.md
    Updated link for sherpa shorter arm
2023-10-23 Update BOM.md fix typo
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2023-11-16 added Dragon Ace HE mounts
    [Klicky-Dock-Mount-shorter_Y.stl]
2023-11-16 fix printing.md HE mount table
2023-11-19 Pandoras Box Carriage STLs to Experimental
    [Belt Clip - Pandora - E [x2].stl, Belt Clip - Pandora - S [x2].stl, Xol Carriage - Front - Pandora - MGN9H - 6mm.stl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]
2023-12-18 experimental mgn12-9mm carriage parts
    [Belt Clip - Pandora - E [x2].stl, Belt Clip - Pandora - S [x2].stl, Xol Carriage - Front - Pandora - MGN9H - 6mm.stl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]
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2023-12-22 Fix typo in printing.md
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2024-01-05 Update Xol-Toolhead_Ducts.step
    fixed internal bridge on ducts.
2024-01-05 fixed internal bridge in ducts
    removed an extra face that was making the bridge have an angle.
    [Xol Ducts - Tri-Vane Asym Left.stl, Xol Ducts - Tri-Vane Asym Right - Trident.stl, Xol Ducts - Tri-Vane Asym Right.stl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]
2024-01-14 added Beacon Rev H modules
    [Beacon_H_Module.stl, Beacon_H_Module_UHF.stl]
2024-01-14 Beacon H included in CAD
    [Xol-HE_Mounts[20231212] - Dragon-Ace.step]
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2024-01-20 NF-Crazy HE mount update + tiny HE mount bug fix on other HE mounts
    [Xol HE Mount - Dragon SF.stl, Xol HE Mount - Dragon SF_fanHS.stl, Xol HE Mount - Next-G.stl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]
2024-01-21 fix duct CAD file
2024-02-23 remove next-g mounts that were based on invalid pre-release CAD
    [Xol HE Mount - Next-G.stl, Xol HE Mount - Next-G_fanHS.stl]
2024-02-25 Added WWG2 extruder mount and updated docs
    [WWG2 front for Xol Extruder Mount.step, WWG2 front for Xol Extruder Mount.stl]
2024-02-25 fixed WWG2 links in printing.md
2024-03-01 experimental pandor mgn9 carriage
    [Xol Carriage - Front - Pandora - MGN9H - 6mm.stl, Xol Carriage - Rear - Pandora - MGN9H - 6mm.stl]
2024-03-06 Add WW BMG to supported extruders with custom front
    [WWBMG front for Xol Extruder Mount.stl]
2024-03-08 Move experimental pre-release to AHI repo (#30)
    * Experimental pre-release STLs
    * update experimental README.md
    * updated xol-carriage experimental STLs
    * Added XG mounts
    * fix missing support on XG mounts
    * STL update for pre-release Xol
    * add probe wire channel to experimental carriages
    * Update README.md
    * update some beta STLs
    * updated pre-release HE mount/duct STLs
    [Beacon_H_Module.stl, Beacon_H_Module_UHF.stl, Beacon_Module.stl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]
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2024-03-13 fix typo's in carriage doco
2024-03-16 fix bug in UHF LED ducts
    [Xol LED Ducts UHF - Tri-Vane Asym Left.stl, Xol LED Ducts UHF - Tri-Vane Asym Right - Trident.stl, Xol LED Ducts UHF - Tri-Vane Asym Right.stl]
2024-04-03 Fix Issue #34 - Trident LED duct missing cutout
    [Xol Ducts - Tri-Vane Asym Left.stl, Xol Ducts - Tri-Vane Asym Right - Trident.stl, Xol Ducts - Tri-Vane Asym Right.stl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]
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2024-06-21 Fix Xol-Carriage filenames in CAD
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2024-08-06 Fix typo in printing.md (#44)
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2024-08-25 Upload EBB mounts step
    [Xol-Carriage_EBB_Mounts.step]
2024-10-19 Minor bugfix: All HE Mounts
    [Xol_HE_Mount-Dragon-Ace_Extender_XolPAP.step, Xol_HE_Mount-Dragon-Ace_XolPAP.step, Xol_HE_Mount-DragonSF-HF_XolPAP.step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]
2024-10-30 upload PFA xol carriage STLs
    [Xol-Carriage_MGN9H_PFA.stl, [a]_belt_clamp_6mm_PFA_x2.stl.stl]
2024-11-02 update PFA Xol-Carriage STL
    [Xol-Carriage_MGN9H_PFA.stl]
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2024-11-02 fix PFA belt clip stl filename
    [[a]_belt_clamp_6mm_PFA_x2.stl]
2024-11-03 PFA carriage with clearance for flipped gantry and no x endstop on toolhead.
    [Xol-Carriage_MGN9H_PFA-No_X_Endstop.stl]
2024-11-12 updated Beacon Rev D probe modules
    [Beacon_Module.stl, Beacon_Module_UHF.stl]
2025-01-01 Add EBB mounts for WWBMG extruder (#57)
    * Updated EBB mount stp file with WWBMG mounts
    - mirror the whole mount across the vertical axis
    - move the lower hole hole slightly for alignment with motor standoff
    - move the 3rd mounting point over slightly for alignment with carriage
    * Added stl files for WWBMG EBB mount
    - start with orbiter 2.0 mount
    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
    [EBB36 Mount - WWBMG.stl, EBB36 Mount -WWBMG [strain relief].stl, Xol-Carriage_EBB_Mounts.step]
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2025-01-15 Update beacon probe modules and include carriage for ants CAD
    [Beacon_Dual_Board_Module.stl, Beacon_Dual_Board_Module_UHF.stl, Beacon_H_Module.stl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]
2025-01-16 upload belt clip parts STEP
    [Xol-Carriage Belt Clip Parts.step]
2025-01-23 added WW-BMG with Sherpa-mini spacing extruder adapters
    [Xol Extruder Mount - WW-BMG [Sherpa-Mini Spacing] - TAP.3mf, Xol Extruder Mount - WW-BMG [Sherpa-Mini Spacing].3mf]
2025-01-25 added basic belts xol-carriage version STL
    [Xol-Carriage_MGN12H_6mm_basic_belts.stl]
2025-01-25 Fix support and add belt helper for basic belts xol-carriage
    [Xol-Carriage_MGN12H_6mm_basic_belts.stl]
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2025-03-01 Revo-Voron HE mounts - make compatible with M3x8 SHCS mounting screws
    [Xol_HE_Mount-Revo-Voron_XolPAP.step]
2025-05-14 rename beacon probe modules
    [Beacon_RevD+Cartographer_Module.stl, Beacon_RevD+Cartographer_Module_UHF.stl, Beacon_RevH_Module.stl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]

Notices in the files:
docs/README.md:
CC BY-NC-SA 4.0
